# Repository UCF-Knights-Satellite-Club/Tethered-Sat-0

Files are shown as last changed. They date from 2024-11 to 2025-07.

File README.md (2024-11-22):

tsat
# Tethered-Sat-0
Tethered-Sat-0 or T-Sat-0 is Knights Satellite Club's first CubeSat mission. This a suborbital, tethered balloon mission.

## Hardware
This mission uses one PCB which has been designed in Autodesk EAGLE. The PCB holds several breakout boards, connectors, and an ESP32 devkit for ease of design and testing. The PCB fits into a 1U frame along with an Arducam Mega, a battery, and a parachute deployment system. The burn-wire system consists of two RFM radio modules, one flies with the CubeSat and recieves the signal from the ground station which sends the burn command. Once the burn command is recieved, a Seeduino XIAO will activate a transistor connected to a nichrome wire which melts through a monofilament fishing line and drops T-Sat-0.

## Software
This project utilizes the Arduino ecosystem on a **DOIT ESP32 DEVKIT V1** and two **Seeeduino XIAO**s. Unless stated otherwise, all libraries can be found in the Arduino IDE Library Manager.

### Prerequisites
- **Arduino ESP32 Core** ([installation instructions](https://docs.espressif.com/projects/arduino-esp32/en/latest/installing.html))
- **Seeeduino Arduino IDE Support** ([installation instructions](https://wiki.seeedstudio.com/Seeed_Arduino_Boards/))
- **Radiohead** by Mike McCauley (Arduino IDE Library Manager version is old, [download directly](http://www.airspayce.com/mikem/arduino/RadioHead/))
- **Adafruit MMA8451 Library** by Adafruit
- **Adafruit BMP3XX Library** by Adafruit
- **Adafruit GFX Library** by Adafruit
- **Adafruit SSD1306** by Adafruit
- **Arducam_Mega** by Arducam
- **ESP32Servo** by Kevin Harrington

### Explanation
The flight software has five states. The first state is `CALIBRATION` which averages several altitude readings to determine a launch altitude. Next is `PREFLIGHT` which runs when T-Sat-0 is on the ground and waiting to be released on the balloon. High acceleration or breaking an altitude threshold will move to the `ASCENT` state. In this state, T-Sat-0 monitors acceleration to determine when it is in free fall. In free fall, the accelerometer will read close to zero. Once this condition is met, the state moves to `FREEFALL` where altitude is compared to the deployment altitude. Once deployment altitude is reached, the parachute is deployed and the state switches to `LANDING`.

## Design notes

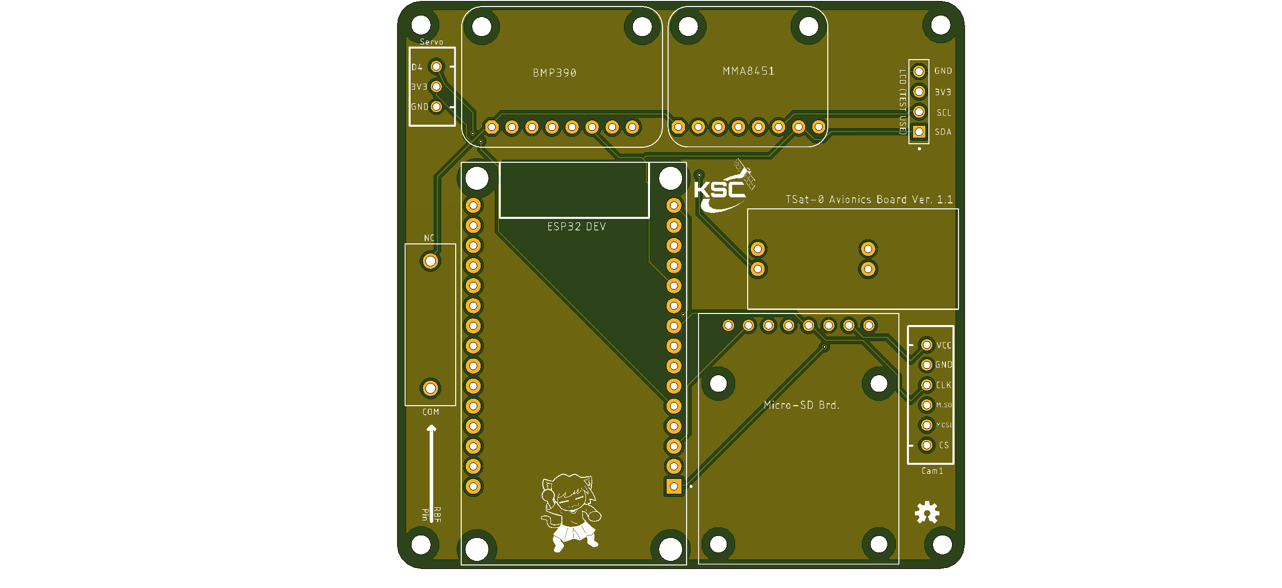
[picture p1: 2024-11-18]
hardware/PCB-Design/Version1.1/TSat0-AvionicsPCB-3D v8.png

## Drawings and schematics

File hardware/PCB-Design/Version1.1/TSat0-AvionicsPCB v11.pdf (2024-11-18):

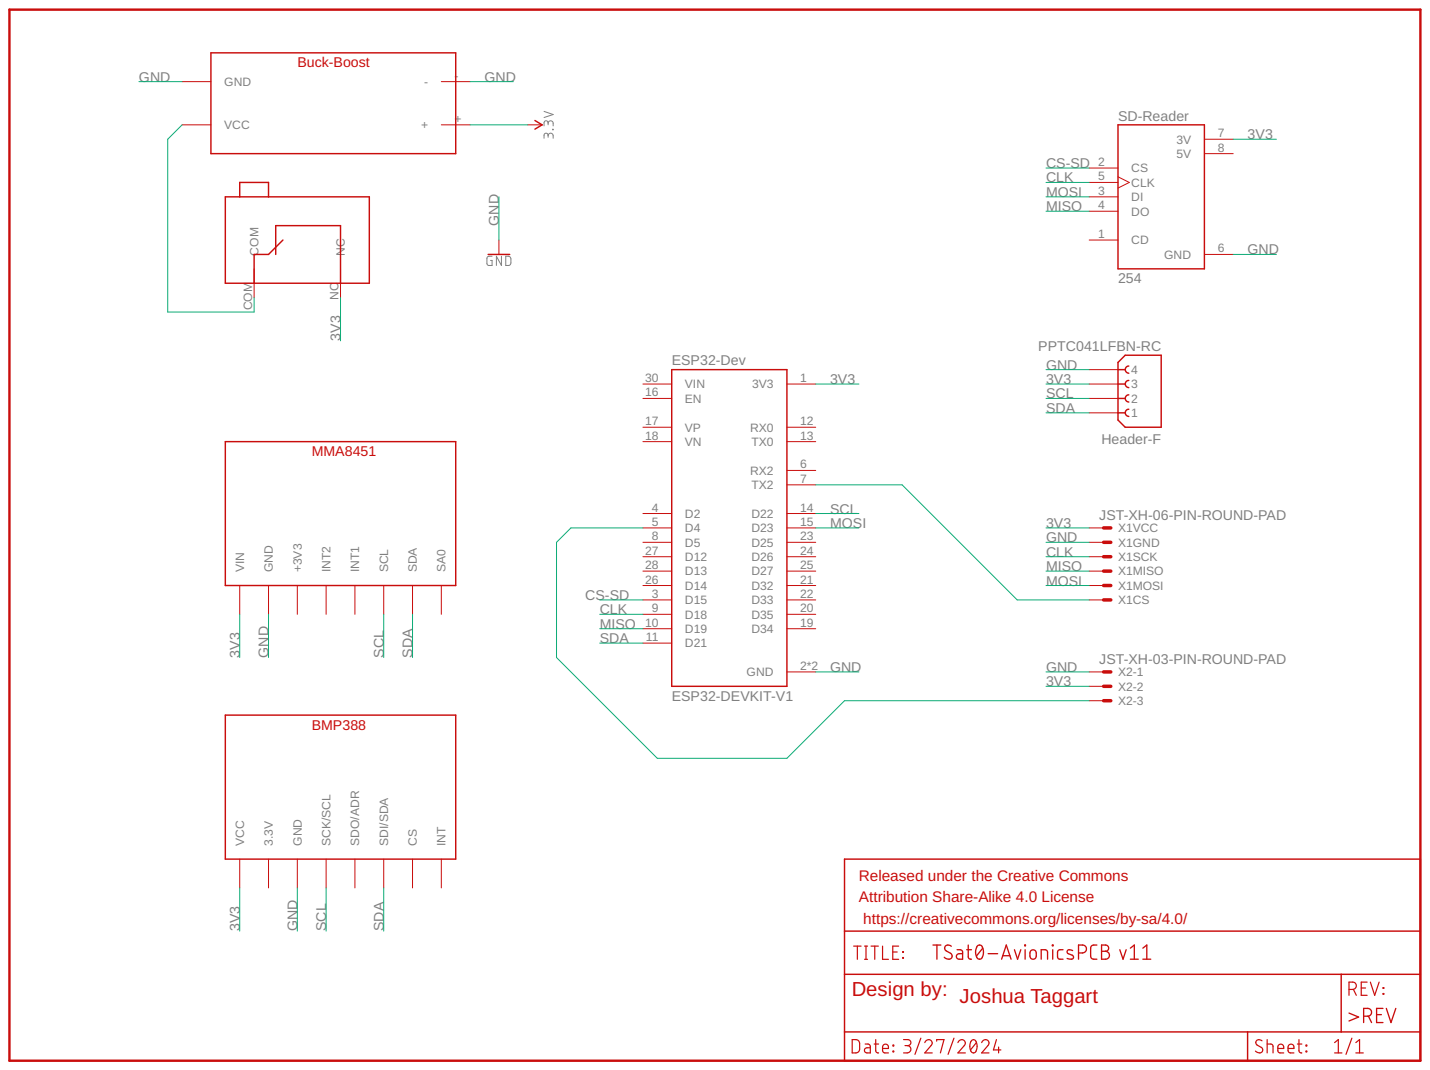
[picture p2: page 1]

JST-XH-03-PIN-ROUND-PAD

SCK/SCL SDO/ADR

Released under the Creative Commons Attribution Share-Alike 4.0 License

https://creativecommons.org/licenses/by-sa/4.0/

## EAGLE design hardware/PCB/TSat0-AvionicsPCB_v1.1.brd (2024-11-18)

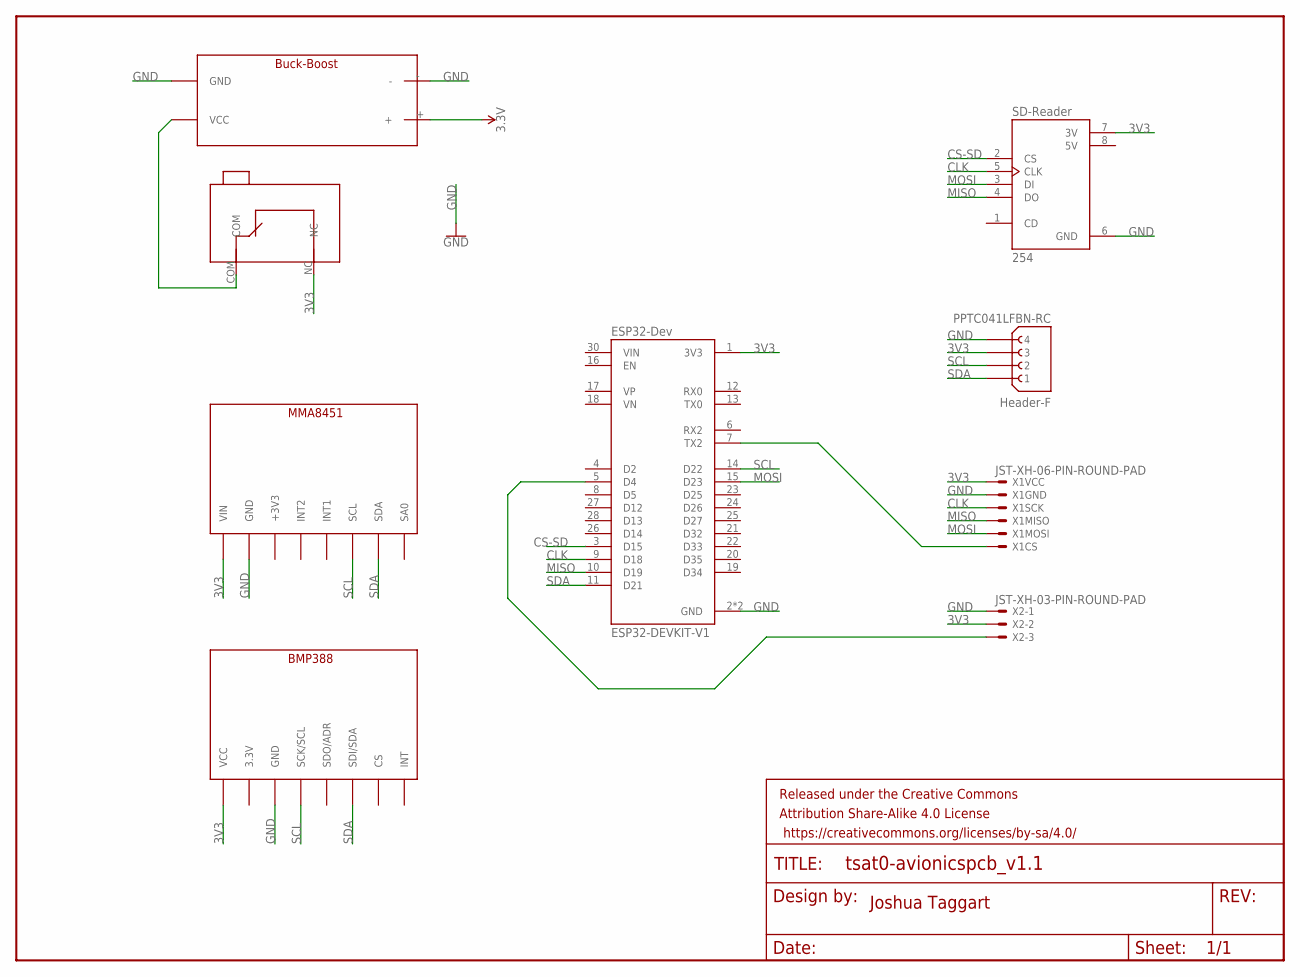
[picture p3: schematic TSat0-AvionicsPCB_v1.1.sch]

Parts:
BMP388: BMP388; BMP388-FP
FRAME1: FRAME-LETTERNO_PACKAGE; DUMMY
J1: PPTC041LFBN-RC; SULLINS_PPTC041LFBN-RC
MMA8451: MMA8451; MMA8451-FP
U1: ESP32-DEVKIT-V1; MODULE_ESP32_DEVKIT_V1
U2: 254; MODULE_254
U$1: BUCKBOOST-LIPO; BUCKBOOST-FP
U$2: OMRON-MICROSWITCH; OMRON-MICROSWITCH-FP
X1: JST-XH-06-PIN-ROUND-PAD; JST-XH-06-PACKAGE-ROUND-PAD
X2: JST-XH-03-PIN-ROUND-PAD; JST-XH-03-PACKAGE-ROUND-PAD

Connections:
3.3V: U$1.+
3V3: BMP388.VCC, J1.3, MMA8451.VIN, U1.1 (3V3), U2.7 (3V), U$2.NC, X1.VCC, X2.2
5V: U2.8 (5V)
CLK: U1.9 (D18), U2.5 (CLK), X1.SCK
CS-SD: U1.3 (D15), U2.2 (CS)
GND: BMP388.GND, J1.4, MMA8451.GND, U1.2 (GND), U1.29 (GND), U2.6 (GND), U$1.-, U$1.GND, X1.GND, X2.1
MISO: U1.10 (D19), U2.4 (DO), X1.MISO
MOSI: U1.15 (D23), U2.3 (DI), X1.MOSI
unnamed: U1.7 (TX2), X1.CS
unnamed: U$1.VCC, U$2.COM
unnamed: U1.5 (D4), X2.3
SCL: BMP388.SCK/SCL, J1.2, MMA8451.SCL, U1.14 (D22)
SDA: BMP388.SDI/SDA, J1.1, MMA8451.SDA, U1.11 (D21)

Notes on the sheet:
Joshua Taggart

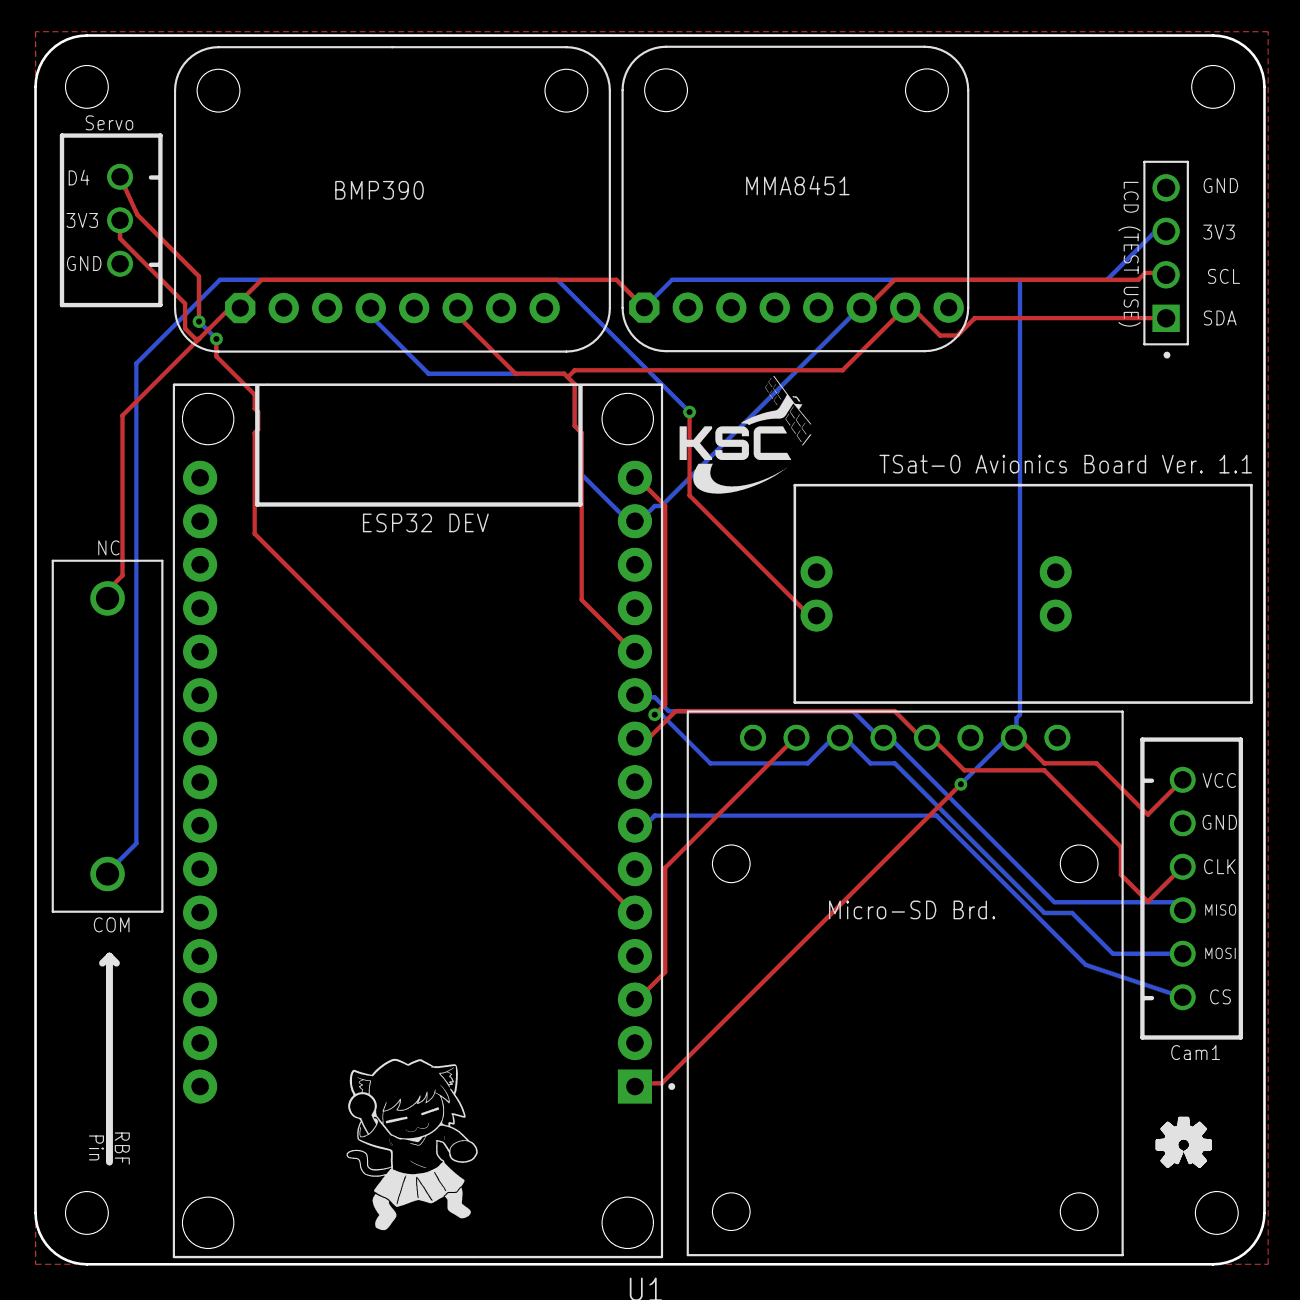
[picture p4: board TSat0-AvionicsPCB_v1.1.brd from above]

Board: 2 copper layers, 71.8 x 71.8 mm, 11 parts (0 on the bottom side), 11 nets.

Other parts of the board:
U$3: OSHW-LOGO-S

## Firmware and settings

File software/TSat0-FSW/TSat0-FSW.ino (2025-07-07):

#include <Wire.h>
#include <Adafruit_MMA8451.h>
#include <Adafruit_Sensor.h>
#include <Adafruit_BMP3XX.h>
#include <Adafruit_GFX.h>
#include <Adafruit_SSD1306.h>
#include <Arducam_Mega.h>
#include <Arducam/Platform.h>
#include <SPI.h>
#include <FS.h>
#include <SD.h>
#include <ESP32Servo.h>
#include <SD.h>
#include <SPI.h>

// Pin constants
#define CAM_CS 17
#define SCK 14
#define MISO 12
#define MOSI 13
#define SD_CS 15
#define SERVO_PIN 4

// Depending on the selected board, may or may not be defined already
#ifndef LED_BUILTIN
#define LED_BUILTIN 2
#endif

// Constants
#define SEALEVELPRESSURE_HPA (1013.25)        // standard pressure at sea level
#define PIC_BUFFER_SIZE 4096                   // buffer size to store images, must be less than 255
#define CAM_IMAGE_MODE CAM_IMAGE_MODE_WQXGA2  // ArduCam image mode
#define SPI_CLOCK_FREQ 16000000               // SPI clock frequency (ArduCAM and SD card)
#define I2C_CLOCK_FREQ 50000                  // I2C clock frequency (BMP and MMA)
#define LOG_QUEUE_SIZE 50                     // how many entries to store before dropping data
#define SPI_MUTEX_WAIT 20                     // how many ms to wait for SPI mutex lock before giving up
#define LOG_DELAY 100                         // how many ms to wait between logging to SD
#define CALIBRATION_COUNT 20                  // how many measurements to average when determining initial altitude
#define ASCENT_ACCEL_THRESHOLD 20             // acceleration above which PREFLIGHT moves to ASCENT
#define MAX_PREFLIGHT_ALTITUDE 5              // altitude where PREFLIGHT automatically switches to ASCENT
#define ALTITUDE_CHECK_DELAY 50               // ms between altitude checks
#define FREEFALL_ACCEL_THRESHOLD 2            // acceleration below which to switch from ASCENT to FREEFALL
#define FREEFALL_VELOCITY_THRESHOLD 5         // decent speed above which to swtich from ASCENT to FREEFALL (FSW=5)
#define PARACHUTE_DEPLOY_ALTITUDE 80          // altutude to switch from FREEFALL to LANDING (FSW=80)
#define ALTITUDE_DELTA_FILTER_GAIN 0.95       // between 0 and 1, higher number means each measurement has lower impact on estimate
#define ACCEL_FILTER_GAIN 0.5                 // same as altitude
#define SERVO_STOW_POS 110                    // initial servo position
#define SERVO_DEPLOY_POS 180                  // parachute deploy position

// Define TEST_MODE to enable test mode
// #define TEST_MODE

// Peripheral globals
Adafruit_MMA8451 mma = Adafruit_MMA8451();
Adafruit_BMP3XX bmp;
#ifdef TEST_MODE
Adafruit_SSD1306 display(128, 64, &Wire, -1);  // select reset pin (just set to any unused pin)
#endif
Arducam_Mega cam(CAM_CS);
Servo servo;
SPIClass *spi = &SPI;

// Function definitions
void write_pic(Arducam_Mega &cam, File dest);
void calibrationRun();
void preflightRun();
void ascentRun();
void freefallRun();
void landingRun();
void checkAltitude(void *parameter);
void cameraCapture(void *parameter);
void logData(void *parameter);

// Globals
static TaskHandle_t check_altitude;
static TaskHandle_t log_data;
static TaskHandle_t camera_capture;
static SemaphoreHandle_t spi_mutex;
static QueueHandle_t log_queue;
bool sd_fail = false;
int pic_num = 0;
char base_dir[20];
float start_altitude = 0;
int calibration_count = 0;
float altitude_delta_estimate = 0;
float prev_altitude_delta_estimate = 0;
float accel_x_estimate = 0;
float prev_accel_x_estimate = 0;
float accel_y_estimate = 0;
float prev_accel_y_estimate = 0;
float accel_z_estimate = 0;
float prev_accel_z_estimate = 0;
float accel_magnitude = 0;
float absolute_altitude = 0;
float ground_altitude = 0;
float altitude_delta = 0;
float prev_altitude = 0;
char logpath[35];
int logindex = 0;
uint8_t image_buf[PIC_BUFFER_SIZE] = {0};

// Describes current flight state
typedef enum {
  CALIBRATION,  // establishing altitude baseline
  PREFLIGHT,    // waiting for launch
  ASCENT,       // rising on balloon
  FREEFALL,     // detached from balloon
  LANDING,      // parachute deployed
} FlightState;

// All the data that gets logged
typedef struct {
  int index;
  double temperature;
  double pressure;
  float altitude;
  float accel_x;
  float accel_y;
  float accel_z;
  float accel_filtered;
  float ascent_velocity_filtered;
  FlightState flight_state;
} DataPoint;

FlightState flight_state = CALIBRATION;

void setup() {
  // LED on for entire setup process
  pinMode(LED_BUILTIN, OUTPUT);
  digitalWrite(LED_BUILTIN, HIGH);

  // init serial
  Serial.begin(115200);

  Wire.begin();
  Wire.setClock(50000);

  // setup OLED if test mode is enabled
  #ifdef TEST_MODE
    display.begin(SSD1306_SWITCHCAPVCC, 0x3c);  // i2c address
    display.setTextSize(2);
    display.setTextColor(WHITE);
  #endif

  // setup MMA
  Serial.println("Starting MMA");
  if (!mma.begin()) {
    Serial.println("Couldnt start MMA");
    while (1) {}
  }
  mma.setRange(MMA8451_RANGE_2_G);
  
  // setup BMP
  Serial.println("Starting BMP");
  if (!bmp.begin_I2C()) {  // hardware I2C mode, can pass in address & alt Wire
    Serial.println("Couldn't start BMP");
    while (1) {}
  }

  // Set up oversampling and filter initialization
  bmp.setTemperatureOversampling(BMP3_OVERSAMPLING_8X);
  bmp.setPressureOversampling(BMP3_OVERSAMPLING_4X);
  bmp.setIIRFilterCoeff(BMP3_IIR_FILTER_COEFF_3);
  bmp.setOutputDataRate(BMP3_ODR_50_HZ);

  // Preload data into bmp
  bmp.performReading();

  // init servo
  Serial.println("Starting servo");
  servo.attach(SERVO_PIN);
  servo.write(SERVO_STOW_POS);

  // init ArduCam, must be done before SD setup so CS lines are configured properly
  Serial.println("Starting cam");
  cam.begin();

  // setup SD
  Serial.println("Starting SD");
  if (!SD.begin(SD_CS, *spi, SPI_CLOCK_FREQ)) {
    Serial.println("Card mount failed");
    sd_fail = true;
  } else if (SD.cardType() == CARD_NONE) {
    Serial.println("No SD card attached");
    sd_fail = true;
  }

  // Queues data to be logged to SD
  log_queue = xQueueCreate(20, sizeof(DataPoint));
  if (log_queue == NULL) {
    Serial.print("Unable to create log queue");
    while (1) {}
  }

  // Used to prevent simultaneous SPI access from causing problems
  spi_mutex = xSemaphoreCreateMutex();
  if (spi_mutex == NULL) {
    Serial.print("Unable to create SPI mutex");
    while (1) {}
  }

  // Must be called after setting up SD and ArduCam since they will reset this
  SPI.setFrequency(SPI_CLOCK_FREQ);

  if (!sd_fail) {
    // Pick base directory for this flight
    int i = 0;
    do {
      sprintf(base_dir, "/tsatlog%d", i);
      i++;
    } while (SD.exists(base_dir));
    SD.mkdir(base_dir);
    Serial.print("Data from this run stored in ");
    Serial.println(base_dir);
    sprintf(logpath, "%s/data.csv", base_dir);

    // Write CSV header
    File log_file = SD.open(logpath, FILE_WRITE);
    if (log_file) {
      log_file.println("index,temp,pressure,altitude,accelx,accely,accelz,accel_filtered,ascent_velocity,state");
      log_file.close();
    }
  }

  Serial.println("Creating tasks");

  // Create task for sensor checks
  xTaskCreatePinnedToCore(
    checkAltitude,     // Function to call
    "Check Altitude",  // Task name
    4096,              // Memory allocated
    NULL,              // Parameters to pass to the function
    2,                 // Priority (higher number = higher priority)
    &check_altitude,   // Task handle
    0                  // Core
  );

  // Create task for taking pictures
  xTaskCreatePinnedToCore(
    cameraCapture,
    "Camera Capture",
    4096,
    NULL,
    tskIDLE_PRIORITY,  // Lowest possible priority, see   
    &camera_capture,
    0
  );

  // Create task for logging data to SD
  xTaskCreatePinnedToCore(
    logData,
    "Log Data",
    4096,
    NULL,
    1,
    &log_data,
    0
  );

  // Delay to stop first image from being green
  vTaskDelay(500 / portTICK_PERIOD_MS);

  // Unsuspend tasks
  Serial.println("Starting tasks");
  vTaskResume(check_altitude);
  if (!sd_fail) {
    vTaskResume(camera_capture);
    vTaskResume(log_data);
  }

  // LED off once setup complete
  digitalWrite(LED_BUILTIN, LOW);
}

// Empty loop function, all functionality in custom tasks
void loop() {
  vTaskDelay(1000 / portTICK_PERIOD_MS);
}

// Periodically monitors sensor data and performs state switches
void checkAltitude(void *parameter) {
  vTaskSuspend(NULL); // Initially suspend task
  
  TickType_t last_wake = xTaskGetTickCount();

  while (1) {
    /*
    Serial.print("absolute alt: ");
    Serial.println(absolute_altitude);
    Serial.print("start alt: ");
    Serial.println(start_altitude);
    Serial.print("alt: ");
    Serial.println(ground_altitude);
    */

    // Get altitude data
    bmp.performReading();
    absolute_altitude = calculateAltitude(bmp.pressure);
    ground_altitude = absolute_altitude - start_altitude;
    altitude_delta = absolute_altitude - prev_altitude;
    prev_altitude = absolute_altitude;

    // Get imu data
    mma.read();
    float accel_x = mma.x_g * SENSORS_GRAVITY_STANDARD;
    float accel_y = mma.y_g * SENSORS_GRAVITY_STANDARD;
    float accel_z = mma.z_g * SENSORS_GRAVITY_STANDARD;

    // Lowpass filter, smoothes out noisy data
    altitude_delta_estimate = (ALTITUDE_DELTA_FILTER_GAIN * prev_altitude_delta_estimate) + (1 - ALTITUDE_DELTA_FILTER_GAIN) * altitude_delta;
    prev_altitude_delta_estimate = altitude_delta_estimate;

    accel_x_estimate = (ACCEL_FILTER_GAIN * prev_accel_x_estimate) + (1 - ACCEL_FILTER_GAIN) * accel_x;
    prev_accel_x_estimate = accel_x_estimate;

    accel_y_estimate = (ACCEL_FILTER_GAIN * prev_accel_y_estimate) + (1 - ACCEL_FILTER_GAIN) * accel_y;
    prev_accel_y_estimate = accel_y_estimate;

    accel_z_estimate = (ACCEL_FILTER_GAIN * prev_accel_z_estimate) + (1 - ACCEL_FILTER_GAIN) * accel_z;
    prev_accel_z_estimate = accel_z_estimate;


    accel_magnitude = sqrtf(accel_x_estimate * accel_x_estimate + accel_y_estimate * accel_y_estimate + accel_z_estimate * accel_z_estimate);

    /*
    Serial.print("accel:");
    Serial.println(accel_estimate);
    */

    // Core state machine
    switch (flight_state) {
      case CALIBRATION:
        /* CALIBRATE: averages measurements to
       * determine a launch altitude. */
        calibrationRun();
        break;
      case PREFLIGHT:
        /* PRE-LAUNCH: waiting on the ground to be released. Detects
       * launch by breaking an altitude rate of change threshold
       * or passing a certain altitude.       - > ASCENT         */
        preflightRun();
        break;
      case ASCENT:
        /* ASCENT: Rising up to the extent of the tether and waiting
       * for the burn wire to trigger and free fall to begin.
       * Detects this by breaking an altitude rate of change
       * threshold (or accelerometer info)    - > FREEFALL       */
        ascentRun();
        break;
      case FREEFALL:
        /* FREE FALL: falling through the air and waiting to
       * hit the parachute deployment altitude.  - > LANDING      */
        freefallRun();
        break;
      case LANDING:
        /* LANDING: Deploy parachute. Final State. */
        landingRun();
        break;
    }

    if (!sd_fail) {
      if (uxQueueSpacesAvailable(log_queue) >= 1) {
        DataPoint data_point = {
          logindex,
          bmp.temperature,
          bmp.pressure,
          ground_altitude,
          accel_x,
          accel_y,
          accel_z,
          accel_magnitude,
          altitude_delta_estimate * 1000 / ALTITUDE_CHECK_DELAY,
          flight_state
        };
        if (xQueueSendToBack(log_queue, &data_point, 0) == pdFALSE) {
          Serial.println("Failed to add data to queue");
        }
      } else {
        Serial.println("WARNING: Log queue is full, some data is getting dropped");
      }

      logindex++;
    }

    #ifdef TEST_MODE
      // display code:
      display.clearDisplay();
      display.drawRoundRect(0, 0, 128, 64, 8, WHITE);
      display.setRotation(2);
      display.setCursor(15, 3);
      if (flight_state != CALIBRATION) {
        display.setCursor(altitude >= 0 ? 22 : 10, 8);
        display.print(altitude);
      } else {
        display.setCursor(absolute_altitude >= 0 ? 22 : 10, 8);
        display.print(absolute_altitude);
      }
      display.print(" m");
      display.setCursor(altitude_delta_estimate >= 0 ? 22 : 10, 28);
      display.print(altitude_delta_estimate * 1000 / ALTITUDE_CHECK_DELAY);
      display.print(" m/s");

      display.setCursor(10, 48);
      switch (flight_state) {
        case CALIBRATION:
          display.print("CALIBRATE");
          break;
        case PREFLIGHT:
          display.print("PREFLIGHT");
          break;
        case ASCENT:
          display.print("ASCENT");
          break;
        case FREEFALL:
          display.print("FREEFALL");
          break;
        case LANDING:
          display.print("LANDING");
          break;
      }
      display.display();
    #endif
    vTaskDelayUntil(&last_wake, ALTITUDE_CHECK_DELAY / portTICK_PERIOD_MS);
  }
}

void cameraCapture(void *parameter) {
  vTaskSuspend(NULL); // Initially suspend task
  while (1) {
    Serial.println("Taking picture");
    cam.takePicture(CAM_IMAGE_MODE, CAM_IMAGE_PIX_FMT_JPG);
    char fp[35];
    sprintf(fp, "%s/pic%d.jpg", base_dir, pic_num);
    pic_num++;
    Serial.println("Saving picture");
    if (xSemaphoreTake(spi_mutex, SPI_MUTEX_WAIT) == pdTRUE) {
      File file = SD.open(fp, FILE_WRITE);
      xSemaphoreGive(spi_mutex);
      write_pic(cam, file);
      Serial.print("Picutre saved to ");
      Serial.println(fp);
    }
  }
}

void logData(void *parameter) {
  vTaskSuspend(NULL); // Initially suspend task
  while (1) {
    if (uxQueueMessagesWaiting(log_queue) > 0) {
      if (xSemaphoreTake(spi_mutex, SPI_MUTEX_WAIT) == pdTRUE) {
        File log_file = SD.open(logpath, FILE_APPEND);
        if (log_file) {
          DataPoint data_point;
          while (xQueueReceive(log_queue, &data_point, 0) == pdTRUE) {
            log_file.print(data_point.index);
            log_file.print(",");
            log_file.print(data_point.temperature);
            log_file.print(",");
            log_file.print(data_point.pressure);
            log_file.print(",");
            log_file.print(data_point.altitude);
            log_file.print(",");
            log_file.print(data_point.accel_x);
            log_file.print(",");
            log_file.print(data_point.accel_y);
            log_file.print(",");
            log_file.print(data_point.accel_z);
            log_file.print(",");
            log_file.print(data_point.accel_filtered);
            log_file.print(",");
            log_file.print(data_point.ascent_velocity_filtered);
            log_file.print(",");
            log_file.println(data_point.flight_state);
          }
          log_file.close();
        } else {
          Serial.println("Error opening file");
        }
        xSemaphoreGive(spi_mutex);
      }
    }
    vTaskDelay(LOG_DELAY / portTICK_PERIOD_MS);
  }
}

/* ==== UTILITY FUNCTIONS ==== */

void write_pic(Arducam_Mega &cam, File dest) {
  uint8_t prev_byte = 0;
  uint8_t cur_byte = 0;
  uint8_t head_flag = 0;
  unsigned int i = 0;
  int read_len = 0;
  int start_offset = 0;
  int bytes_written = 0;

  while (cam.getReceivedLength()) {
    read_len = 0;

    // Fill image_buf in chunks
    while (read_len < PIC_BUFFER_SIZE && cam.getReceivedLength()) {
      uint32_t chunk_len = min(254, PIC_BUFFER_SIZE - read_len);
      if (xSemaphoreTake(spi_mutex, SPI_MUTEX_WAIT) == pdTRUE) {
        uint32_t actual_read = cam.readBuff(image_buf + read_len, chunk_len);
        xSemaphoreGive(spi_mutex);

        if (actual_read == 0) {
          break; // No more data
        }
        read_len += actual_read;
      } else {
        Serial.println("WARNING: SPI lock timeout exceeded");
        return;
      }
    }

    start_offset = 0;

    for (i = 0; i < read_len; i++) {
      prev_byte = cur_byte;
      cur_byte = image_buf[i];

      if (prev_byte == 0xff && cur_byte == 0xd8) {
        Serial.print("Found jpeg start at i=");
        Serial.println(i);
        head_flag = 1;
        start_offset = i + 1;
        if (xSemaphoreTake(spi_mutex, SPI_MUTEX_WAIT) == pdTRUE) {
          bytes_written += dest.write(0xff);
          bytes_written += dest.write(0xd8);
          dest.flush();
          xSemaphoreGive(spi_mutex);
        } else {
          Serial.println("WARNING: SPI lock timeout exceeded");
          return;
        }
      }

      if (head_flag && prev_byte == 0xff && cur_byte == 0xd9) {
        Serial.print("Found jpeg end at i=");
        Serial.println(i);
        Serial.print("Writing buffer from ");
        Serial.print(start_offset);
        Serial.print(" with len ");
        Serial.println(i + 1 - start_offset);
        if (xSemaphoreTake(spi_mutex, SPI_MUTEX_WAIT) == pdTRUE) {
          bytes_written += dest.write(image_buf + start_offset, i + 1 - start_offset);
          dest.close();
          xSemaphoreGive(spi_mutex);
        } else {
          Serial.println("WARNING: SPI lock timeout exceeded");
        }
        Serial.print(bytes_written);
        Serial.println(" total bytes written");
        return;
      }
    }

    if (head_flag) {
      if (xSemaphoreTake(spi_mutex, SPI_MUTEX_WAIT) == pdTRUE) {
        int retval;
        retval = dest.write(image_buf + start_offset, read_len - start_offset);
        /*
        For some reason, writes occasionally fail with dest.write() returning 0. Once that happens,
        all subsequent writes will also fail and return 0. Only fix I could find was to close and
        reopen the file. When opened, the file needs to be seeked to the end.
        */
        if (retval == 0) {
          char fp[35];
          strcpy(fp, dest.path());
          dest.close();
          dest = SD.open(fp, FILE_WRITE);
          dest.seek(dest.size());
          Serial.print("Write fail! Reopened ");
          Serial.println(fp);
          bytes_written += dest.write(image_buf + start_offset, read_len - start_offset);
        }
        bytes_written += retval;
        dest.flush();
        xSemaphoreGive(spi_mutex);
      } else {
        Serial.println("WARNING: SPI lock timeout exceeded");
        return;
      }
    }
  }

  Serial.println("WARNING: No JPEG end flag found, possible corruption");
}

float calculateAltitude(float atmospheric) {
  atmospheric = atmospheric / 100.0;
  return 44330.0 * (1.0 - pow(atmospheric / SEALEVELPRESSURE_HPA, 0.1903));
}

/* ================================= */

/* ==== STATE MACHINE FUNCTIONS ==== */

void calibrationRun() {
  // average several readings for baseline then move to PRELAUNCH
  start_altitude += absolute_altitude;
  calibration_count++;

  Serial.print("Calibrating altitude ");
  Serial.print(calibration_count);
  Serial.print("/");
  Serial.println(CALIBRATION_COUNT);

  if (calibration_count >= CALIBRATION_COUNT) {
    start_altitude /= CALIBRATION_COUNT;
    flight_state = PREFLIGHT;

    Serial.print("Starting altitude: ");
    Serial.println(start_altitude);
    Serial.println("Calibration complete, moving to PREFLIGHT");
  }
}

void preflightRun() {
  // move to ASCENT if acceleration is or altitude above threshold

  if (ground_altitude >= MAX_PREFLIGHT_ALTITUDE) {
    flight_state = ASCENT;
    Serial.println("Max preflight altitude exceeded, moving to ASCENT");

  } /*else if (accel_magnitude >= ASCENT_ACCEL_THRESHOLD) {
    flight_state = ASCENT;
    Serial.println("Acceleration threshold met, moving to ASCENT");
  }*/
}

void ascentRun() {
  // move to FREEFALL if acceleration is close to 0
  /*if (accel_magnitude <= FREEFALL_ACCEL_THRESHOLD) {
    flight_state = FREEFALL;
    digitalWrite(LED_BUILTIN, HIGH);
    Serial.println("Acceleration threshold met, moving to FREEFALL");
  }*/
  // move to FREEFALL if altitude is changing faast enough
  if (altitude_delta_estimate * 1000 / ALTITUDE_CHECK_DELAY < -FREEFALL_VELOCITY_THRESHOLD) {
    flight_state = FREEFALL;
    digitalWrite(LED_BUILTIN, HIGH);
    Serial.println("Decent velocity threshold met, moving to FREEFALL");
  }
}

void freefallRun() {
  // move to LANDING if below deployment altitude
  if (ground_altitude < PARACHUTE_DEPLOY_ALTITUDE) {
    flight_state = LANDING;

    Serial.println("Parachute deployment altitude reached, moving to LANDING");
    servo.write(SERVO_DEPLOY_POS);
  }
}

void landingRun() {
  // Deploy parachute, no more state changes
}

/* ================================= */

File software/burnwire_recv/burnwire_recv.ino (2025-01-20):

#include <SPI.h>
#include <RH_RF95.h>

#define RF95_CS 4
#define RF95_G0 5
#define RF95_RST 6
#define BURN_PIN 2
#define BURN_MS 10000 // Burn time 10 seconds

#define RF95_EN 1
 
// Singleton instance of the radio driver
RH_RF95 rf95(RF95_CS, RF95_G0);
 
uint8_t reply_start[] = "Burning the wire";  // msg back to ground
uint8_t reply_end[] = "Burn completed";  // msg back to ground

void setup() 
{
  Serial.begin(115200);
  Serial.println("Initializing");

  // Disable radio reset
  pinMode(RF95_RST, OUTPUT);
  digitalWrite(RF95_RST, HIGH);

  // run EN pin high (powers on radio)
  pinMode(RF95_EN, OUTPUT);
  digitalWrite(RF95_EN, HIGH);

  if (!rf95.init()) {
    Serial.println("RF95 module initialization failed!");
    while (1);  // Halt if radio initialization fails
  }

  rf95.setFrequency(915.0);  // Set frequency 
  
  pinMode(BURN_PIN, OUTPUT);  // Set the burn pin as output
  digitalWrite(BURN_PIN, LOW);  // burn pin is initially off

  pinMode(LED_BUILTIN, OUTPUT);
  digitalWrite(LED_BUILTIN, HIGH); // LED on xiao is inverted

  Serial.println("T-Sat isready to receive messages.");
}

void loop()
{
  uint8_t buf[RH_RF95_MAX_MESSAGE_LEN];
  uint8_t len = sizeof(buf);

  // Wait for a message from Ground Station
  if (rf95.waitAvailableTimeout(5000)) { 
    //Checks if message was received 
    if (rf95.recv(buf, &len)) 
    {
      // Received a message, print it out and trigger burn action
      Serial.print("Received message: ");
      Serial.println((char*)buf);  // Print the received message

      if (strcmp((char*)buf, "BurnWire") == 0) 
      {
        // Message is "BurnWire", trigger LED and send response
        rf95.send(reply_start, sizeof(reply_start));

        // Disable radio during burn
        //rf95.sleep();

        // power off radio (by pulling EN pin low)
        //digitalWrite(RF95_EN, LOW);
        //delay(2000);

        // Burn!
        digitalWrite(BURN_PIN, HIGH);
        digitalWrite(LED_BUILTIN, LOW);

        Serial.println("Burn wire is ON (burn begin)");

        // Delay for burn duration
        delay(BURN_MS);

        // Turn off the burn wire
        digitalWrite(BURN_PIN, LOW);
        digitalWrite(LED_BUILTIN, HIGH);
        Serial.println("Burn wire is OFF (burn complete)");

        // Wake up radio
        rf95.available();

        // Send response to Ground Station
        Serial.println("Sending reply: 'Burning the wire...'");
        rf95.send(reply_end, sizeof(reply_end));
      }
    } 
    else
    {
      Serial.println("Receive failed");
    }
  } 
  else 
  {
    Serial.println("No message received from Ground Station TEST");
  }
}

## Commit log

2024-03-02 added folders, camera test code
2024-03-27 changed file layout, lora test codes, pcb design filles
    [TSat0-AvionicsPCB_v1.1.brd, TSat0-AvionicsPCB_v1.1.sch]
2024-06-16 fsw for testing work
    [TSat0-AvionicsPCB_v12.sch, TSat0-PCB_v17.brd]
2024-11-18 reorganize repo
    [TSat0-AvionicsPCB_v1.1.brd, TSat0-AvionicsPCB_v1.1.sch, TSat0-AvionicsPCB_v12.sch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]
2024-11-18 remove old files
    [TSat0-AvionicsPCB_v1.1.brd, TSat0-AvionicsPCB_v1.1.sch, TSat0-AvionicsPCB_v12.sch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]
2024-11-18 removed unnecessary functions, fixed compiling
    [TSat0-FSW.ino]
2024-11-18 led indicate software reset
    [servo_test.ino]
2024-11-20 Create burnwire_recv2
    Update burnwire recv radio with the button
2024-11-20 replace old burnwire code
    [burnwire_recv.ino, burnwire_send.ino]
2024-11-21 change freefall detection to use accelerometer
2024-12-04 bring back camera code
2024-12-05 faster image saving, still having corruption issues
    [TSat0-FSW.ino]
2024-12-05 wrap all spi access in mutex
2024-12-06 queue telemetry logs to avoid fighting over mutex
    [TSat0-FSW.ino]
2024-12-06 add comments and fix spacing
    [TSat0-FSW.ino]
2025-01-16 filter accel components seperately
2025-01-16 run altitude checks even if sd mount fails
    [TSat0-FSW.ino]
2025-01-16 remove F() macros, not needed on esp32
2025-01-17 Update burnwire_recv.ino
    testing changes
    [burnwire_recv.ino]
2025-01-18 fix trigger pin
2025-01-18 fix recv and send mixup
    [burnwire_recv.ino, burnwire_send.ino]
2025-01-18 sleep radio during burn
    [burnwire_recv.ino]
2025-01-20 Update burnwire_recv.ino
    burnwire_recv changes
    [burnwire_recv.ino]
2025-06-09 fix i2c errors and image corruption
    [TSat0-FSW.ino]
2025-06-11 major image speedup and corruption fix
    [TSat0-FSW.ino]
2025-06-11 remove accelerometer mode change

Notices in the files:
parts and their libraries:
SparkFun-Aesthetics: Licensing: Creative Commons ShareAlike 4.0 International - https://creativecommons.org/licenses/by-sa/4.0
